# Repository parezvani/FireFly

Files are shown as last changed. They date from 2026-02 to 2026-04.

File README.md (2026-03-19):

# ESP-32-Drone (FireFLY)

FireFLY is a student-built drone platform centered on the `ESP32-C3-DevKit-RUST-1` for fire risk monitoring in areas without existing sensor coverage.

## Need
Remote and high fire-risk areas lack the sensor infrastructure necessary to monitor environmental conditions during the critical pre-fire window, leaving fire response teams without the real-time data needed to act early.

## Goal
Provide fire response teams with real-time temperature, humidity, and smoke readings from high-risk, infrastructure-free terrain by deploying a rapidly mobilized monitoring system that transmits real-time data to a ground station and alerts operators when fire risk thresholds are crossed.

## Repository Layout
- `main/`: source code, firmware experiments, and hardware tests.
  - `scripts/`: ESP-NOW communication and control prototypes.
  - `base-server/fire-server/`: Rust ground-station server/client for telemetry.
  - `testing/motor/`: motor test firmware and hardware validation code.
  - `lab4_1/`: earlier lab firmware kept for reference.
  - `scrapped/`: older discarded experiments and scratch files.
- `docs/`: project documentation and design artifacts.
  - `drone-designs/`: CAD models, frame iterations, and dimensions.
  - `circuit-design/`: wiring diagrams, schematics, and circuit photos.
  - `bill-of-materials/`: BoM revisions and pricing snapshots.
  - `design-document/`: LaTeX source and exported design document PDFs.
  - `status-reports/`: progress reports and planning artifacts.
  - `meeting-notes/`: team notes, decisions, and action items.
  - `research-notes/`: reference material gathered during development.
- `esp/esp-idf/`: local checkout of the ESP-IDF framework used by the embedded work.

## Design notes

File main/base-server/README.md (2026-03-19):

FIRE_SERVER:
------------------------------------------------------------------------------------------------------------------------------------------
Sends message using cargo/rust. 
If you want to test this out on your own you can download the "fire_server" directory. 

Open two instances of Ubuntu:
- On one run "cargo run --bin fire_server", 
- On the other run "cargo run --bin fire_server"

Send message from drone to server in the following format:
- Request Line: FIRE /telemetry DRONE/1.0\n
- Telemetry Line: Fire-Detected: yes; Fire-Distance: 120; Fire-Range: 45; Temperature: 63.4; Humidity: 21.5; Drone-ID: DRONE-01\n

Full Payload:
FIRE /telemetry DRONE/1.0\nFire-Detected: yes; Fire-Distance: 120; Fire-Range: 45; Temperature: 63.4; Humidity: 21.5; Drone-ID: DRONE-01\n

------------------------------------------------------------------------------------------------------------------------------------------
------------------------------------------------------------------------------------------------------------------------------------------

ESPNOW DIRECTORIES:
------------------------------------------------------------------------------------------------------------------------------------------
Sends messages between two ESP32c3-devkit-Rust-1 microcontrollers
Uses ESP-IDF

Build and flash fire_bridge on base station esp

Build and flash fire_drone on drone esp

Currently takes temperature and humidity readings from onboard drone ESP IMU and sends them to the base server ESP through ESP-NOW

Same payload construction as fire_server:
FIRE /telemetry DRONE/1.0\nFire-Detected: yes; Fire-Distance: 120; Fire-Range: 45; Temperature: 63.4; Humidity: 21.5; Drone-ID: DRONE-01\n

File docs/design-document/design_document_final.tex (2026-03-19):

\documentclass[journal, onecolumn]{IEEEtran}

\usepackage{titlesec}
\usepackage{graphicx}
\usepackage{array}
\usepackage{makecell}
\usepackage{float}
\usepackage{caption}
\usepackage{wrapfig}

\titleformat{\section}
    {\normalfont\bfseries}
    {\thesection}
    {1em}
    {}

\titleformat{\subsection}
    {\normalfont\bfseries}
    {\thesubsection}
    {1em}
    {}

\renewcommand\thesection{\arabic{section}}
\renewcommand\thesubsection{\thesection.\arabic{subsection}}
\renewcommand\thesubsubsection{\thesubsection.\arabic{subsubsection}}

\begin{document}

\title{FireFly Design Document}
\author{Christian Li, Kenny Wang, Kevin Yao, Matin Sobhani, Nick Lafredo, Parsa Rezvani, Ryan Yu}
\date{\today}

\maketitle

\begin{figure*}[!t]
    \centering
    
    \caption*{}
    \label{fig:UCSCLOGO}
\end{figure*}

\vspace{1in}

\begin{figure*}[!t]
    \centering
    
    \caption*{}
    \label{fig:BELOGO}
\end{figure*}

\clearpage

\tableofcontents

\vspace{1in}

\begin{abstract}
This document presents the design and proof-of-concept for FireFly, a rapidly deployable environmental monitoring drone for wildfire detection in infrastructure-free terrain.
\end{abstract}

\newpage

% ============================================================
\section*{Executive Summary}
\addcontentsline{toc}{section}{Executive Summary}
% ============================================================

FireFly is a rapidly deployable quadcopter designed for first-response
environmental monitoring in high wildfire-risk areas with no existing sensor
infrastructure. The system collects real-time temperature, humidity, and smoke
data and transmits live readings to a ground station, triggering alerts when
fire risk thresholds are crossed.

\vspace{0.5em}

The design centers on a 3D-printed X-frame carrying a dedicated onboard microcontroller, temperature and humidity sensor, and smoke detector. A flight controller manages propulsion and stabilization while the onboard microcontroller handles sensor acquisition and wireless transmission to a ground receiver. A 3S LiPo battery powers both propulsion and electronics for the duration of a monitoring mission.

\vspace{0.5em}

Validation consists of bench testing individual modules (power, propulsion,
sensors, and communications) followed by tethered and open-field flight
testing for stable hover, data link verification, and threshold-based smoke
and temperature detection. The goal is to demonstrate that FireFly can serve
as a practical proof-of-concept for infrastructure-independent wildfire
monitoring.

\clearpage

% ============================================================
\section{Introduction}
% ============================================================

This document contains all the information needed to design and use the FireFly Drone.

\vspace{1em}

Why is collecting data during a pre-fire window important? A pre-fire window, the period before an incident occurs, is critical because it provides time-sensitive information that improves responder safety, reduces property damage, and enables faster, more effective emergency response. Data on vegetation conditions, topography, temperature, humidity, and smoke concentration helps predict fire behavior, identify high-risk areas, and support mitigation actions such as controlled burns or targeted thinning operations. Without this information, emergency crews arrive with incomplete situational awareness and must gather critical details in real time under dangerous conditions.

\vspace{1em}

For wildfire response specifically, the challenge is compounded by geography. High-risk areas are frequently roadless wilderness where permanent sensor infrastructure cannot be installed or maintained. Satellite imagery and aerial patrols provide coverage, but both suffer from response delays and gaps during the highest-risk windows. The result is a critical blind spot: the pre-fire period in remote terrain is precisely where early awareness matters most, yet it is the hardest environment in which to collect data.

\vspace{1em}

FireFly addresses this gap directly. By deploying a sensor-equipped quadcopter into areas with zero existing infrastructure, FireFly enables real-time collection of temperature, humidity, and smoke data during the pre-fire window, transmitting live readings to a ground station and triggering alerts when fire risk thresholds are crossed. The platform is designed for rapid deployment by field crews without requiring extensive training or specialized support, transforming what would otherwise be a period of uncertainty into a structured, data-driven response.

\subsection{Need Statement}
Remote and high fire-risk areas lack the sensor infrastructure necessary to monitor environmental conditions during the critical pre-fire window, leaving fire response teams without the real-time data needed to act early.

\subsection{Goal Statement}
Provide fire response teams with real-time temperature, humidity, and smoke readings from high-risk, infrastructure-free terrain by deploying a rapidly mobilized monitoring system that transmits real-time data to a ground station and alerts operators when fire risk thresholds are crossed.

\subsection{Personas}
Individuals with experience levels ranging from novice to expert in fire monitoring and environmental fieldwork.

\subsubsection*{End Users}

\begin{wrapfigure}{l}{0.2\textwidth}
    
\end{wrapfigure}
\textbf{Marcus} \\
\underline{\textit{Role:}} Wildfire Operations Coordinator (professional first responder) \\
\underline{\textit{Background / Context:}} Works with a state forestry division managing prescribed burns and post-fire monitoring. Needs something fast that he can hand off to field crews without extensive training. \\
\underline{\textit{Goals:}} Rapid deployment of sensor-equipped drones into areas too dangerous or inaccessible for personnel during the high-risk pre-fire window. Wants real-time smoke and temperature data without putting people in harm's way. \\
\underline{\textit{Behaviors:}} Works under time pressure, values reliability over features, and coordinates with multiple agencies. Skeptical of unproven technology. Practical: if it breaks in the field, it needs to be fixable on-site with minimal tools. \\
\underline{\textit{Expectations:}} A rugged, simple-to-operate platform that can be deployed at a moment's notice. Wants clear threshold alerts he can act on immediately.

\vspace{1em}

\begin{wrapfigure}{l}{0.2\textwidth}
    
\end{wrapfigure}
\textbf{Elena} \\
\underline{\textit{Role:}} Ecology Graduate Researcher (academic user) \\
\underline{\textit{Background / Context:}} Studying fire risk and ecosystem conditions at a land-grant university. Needs to collect environmental sensor data across wilderness areas where no permanent monitoring infrastructure exists. Currently hikes in with handheld sensors, which limits how often and how broadly she can sample. \\
\underline{\textit{Goals:}} Automate pre-fire data collection over defined survey areas. Wants live temperature, humidity, and smoke readings logged without requiring physical presence at each site. \\
\underline{\textit{Behaviors:}} Comfortable with technical documentation, participates in academic drone and environmental monitoring communities, and documents everything for publication. Willing to configure and customize but does not have time to build from scratch. \\
\underline{\textit{Expectations:}} A reliable platform with a clear data pipeline she can connect to her existing research database, and results trustworthy enough to cite.

\vspace{1em}

\subsubsection*{Experts / Consultants}

\begin{wrapfigure}{l}{0.2\textwidth}
    
\end{wrapfigure}
\textbf{Dr. Anita Rowe} \\
\underline{\textit{Role:}} Environmental Sensor Systems Engineer \\
\underline{\textit{Background / Context:}} Works at a national lab developing atmospheric sensor arrays for wildfire monitoring. Has deep expertise in what data is actually actionable in pre-fire environments and where sensors fail under heat, humidity, and particulate exposure. \\
\underline{\textit{Goals:}} Validate that FireFly's sensor suite captures meaningful data for fire risk assessment and identify unreliable component choices before they are locked into the design. \\
\underline{\textit{Behaviors:}} Data-driven and skeptical of consumer-grade sensors in harsh field conditions. Will probe calibration drift, operating temperature limits, and whether threshold alert logic reflects real-world fire risk indicators. \\
\underline{\textit{Expectations:}} A platform sound enough in its sensor selection and alert logic that field results can be trusted and the methodology can be defended to other scientists.

\vspace{1em}

\subsubsection*{Client}

\begin{wrapfigure}{l}{0.2\textwidth}
    
\end{wrapfigure}
\textbf{U.S. Forest Service Regional Office} \\
\underline{\textit{Role:}} Federal Land and Fire Management Agency \\
\underline{\textit{Background / Context:}} Responsible for fire prevention, monitoring, and response across millions of acres of national forest, much of it roadless wilderness with no existing sensor infrastructure. Currently relies on satellite imagery, fire lookout towers, and aerial patrols, all of which have coverage gaps and response delays during the highest-risk windows. \\
\underline{\textit{Goals:}} Evaluate FireFly as a rapidly deployable supplement to existing monitoring systems for areas where infrastructure cannot operate. Interested in whether the platform can reliably trigger alerts before a fire establishes. \\
\underline{\textit{Behaviors:}} Evaluates tools based on operational reliability and ease of use for non-specialist field crews. Requires demonstrated performance data before recommending adoption. \\
\underline{\textit{Expectations:}} A working prototype that proves the core concept: zero-infrastructure deployment, live sensor transmission, and threshold-based alerting, with documentation clear enough for field personnel to operate without engineering support.

\subsection{Existing Research}
Current wildfire detection relies on satellite imagery, fixed camera networks,
and manned aircraft. Satellites cannot reliably detect fires smaller than
approximately 18 square kilometers. Fixed towers like AlertCalifornia's
camera network are constrained by line of sight, leaving roadless terrain
uncovered. UAV-based systems have shown promise, with UAV--IoT networks
detecting fires as small as 2.5 square kilometers at over 99 percent accuracy,
but most depend on pre-deployed ground sensors or persistent network
infrastructure that does not exist in remote areas.

\vspace{0.5em}

FireFly addresses this gap by providing a self-contained, rapidly deployable
platform that requires no pre-existing infrastructure to deliver real-time
environmental data and threshold-based fire risk alerts.

\subsection{Sustainability Statement}

The FireFly project is committed to the ``Design for Environment'' philosophy. Our goal is to provide a high-tech solution for wildfire mitigation while ensuring that the lifecycle of the drone itself does not offset its environmental benefits.

\vspace{1em}

\textbf{Environmental Stewardship:}
The primary purpose of FireFly is the preservation of biodiversity and carbon sinks by preventing catastrophic wildfires. By providing early-warning data in the pre-fire window, we reduce the need for large-scale, carbon-intensive emergency responses such as heavy tanker aircraft and ground fleets. Furthermore, by utilizing electric propulsion over internal combustion, we ensure zero-emission operation during monitoring flights.

\vspace{1em}

\textbf{Material Selection and Circularity:}
To minimize our manufacturing footprint, we have opted for 3D-printed components using \textbf{PLA}. PLA is a bio-based, industrially compostable polymer derived from renewable resources like corn starch. By using additive manufacturing, we significantly reduce material waste compared to traditional subtractive machining.

\vspace{1em}

\textbf{Life Cycle and Battery Management:}
We recognize that Lithium-Polymer (LiPo) batteries pose a chemical risk if disposed of improperly. Our operational plan includes a strict end-of-life protocol where degraded cells are discharged and taken to certified e-waste recycling centers. We have designed the electronics with standardized connectors to ensure that sensors and flight controllers can be harvested and reused in future iterations of the platform, extending the functional life of the high-value silicon components.

\vspace{1em}

\textbf{Social and Safety Impact:}
Sustainability includes the protection of human capital. FireFly enhances the safety of first responders by providing situational awareness in hazardous terrains without risking human life. By creating a rapidly deployable tool, we extend access to advanced fire-monitoring capability to smaller forestry divisions and academic researchers who operate outside the reach of satellite-based or manned aerial surveillance programs.

\vspace{1em}

\textbf{Ethics Statement:}
As engineers, we recognize that our work has a direct impact on public safety and the environment. We are committed to upholding the highest standards of honesty, transparency, and responsibility throughout the design and development of FireFly. Our system is intended solely to support fire prevention and responder safety. We will not misrepresent the capabilities of the prototype, will clearly communicate the limitations of sensor accuracy and flight duration, and will ensure that any data collected during testing is handled responsibly. We adhere to the NSPE Code of Ethics, holding paramount the safety, health, and welfare of the public in all design decisions.

% ============================================================
\section{Design}
% ============================================================

\subsection{Design Objectives}
The objective of this project is to develop a robust aerial monitoring platform capable of reliable operation in remote, high-risk environments. To achieve this, the system requires a long-range communication link and high-speed data transmission to ensure low-latency control and real-time environmental telemetry. Furthermore, the power architecture must be optimized to sustain extended monitoring missions.

\newpage

\subsection{Aesthetic Prototype}

The FireFly aesthetic prototype follows a field-ready design language: a compact enclosed central body with rounded corners, symmetric X-arm geometry, and cylindrical motor pods at each corner. The overall form emphasizes structural clarity and quick visual inspection rather than cosmetic styling. Rounded exterior edges reduce snag points during transport, while the open-top bay and side windows communicate where electronics, wiring, and battery hardware are intended to be serviced.

\begin{figure}[H]
    \centering
    
    \hfill
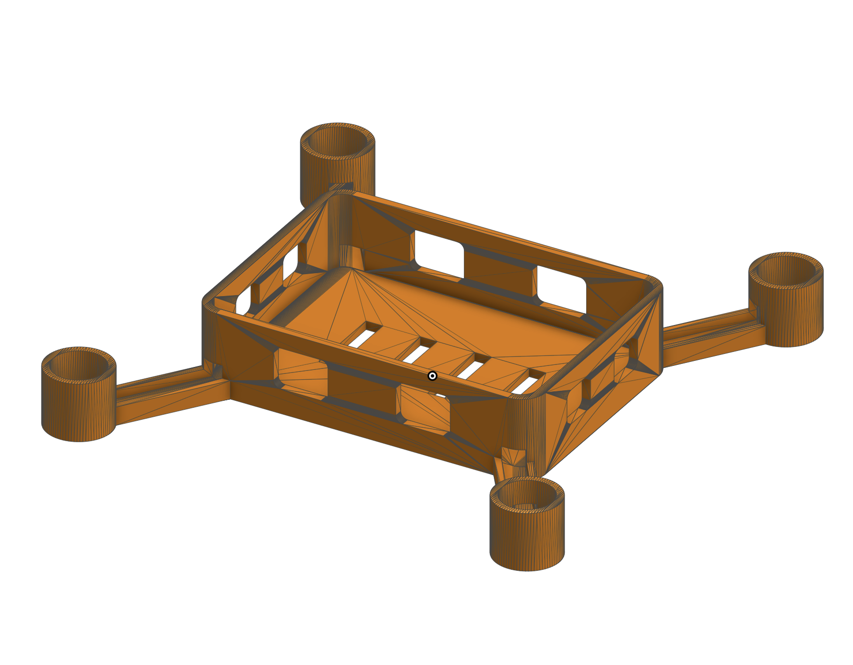
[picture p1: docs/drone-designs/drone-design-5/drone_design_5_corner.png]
    
    \caption{FireFly CAD aesthetic prototype, iteration v5 (top and isometric views).}
    \label{fig:drone_v5_aesthetic}
\end{figure}

The prototype evolved through multiple print-test iterations. Early versions validated basic packaging and motor placement, while later versions introduced a cleaner body-to-arm transition, larger internal volume, and improved vent/window geometry for lighter weight and faster access to internals. This iterative process preserved a consistent visual identity while converging on a more manufacturable and maintainable frame.

\begin{figure}[H]
    \centering
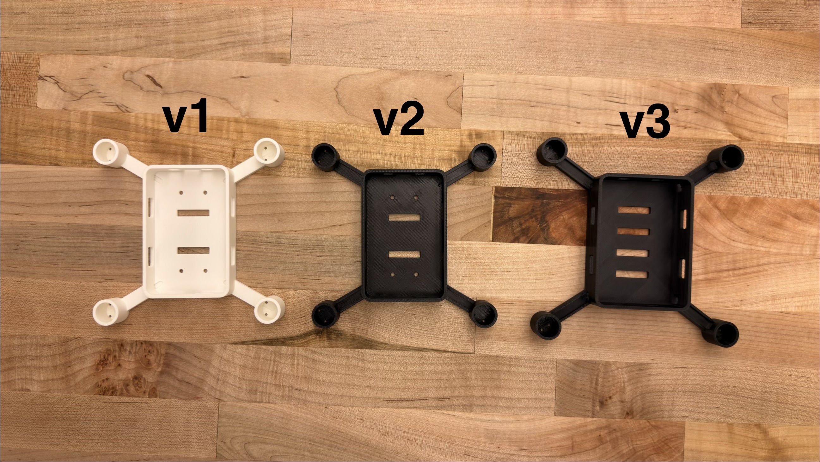
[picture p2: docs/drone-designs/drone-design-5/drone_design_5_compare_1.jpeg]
    
    \caption{Physical prototype progression (v1--v3) that informed the final v5 frame direction.}
    \label{fig:drone_proto_progression}
\end{figure}

\subsection{Design for Manufacture, Assembly, Maintenance}

\textbf{Design for Manufacture (DFM):}
The current frame is designed as a single-piece 3D print to minimize part count and remove alignment errors. The v5 CAD envelope is approximately $100 \times 72 \times 24$ mm with $2.5$ mm floor and wall thicknesses, balancing print speed, stiffness, and mass. Arms are sized at $10.0$ mm width and $5.4$ mm thickness to maintain rigidity under motor thrust and landing loads. Motor pods are dimensioned for SunnySky R1106-class motors with built-in tolerance ($19$ mm outer diameter, $15.0$ mm inner diameter, $17$ mm height, $2.2$ mm mounting holes on a $9$ mm bolt-circle).

\vspace{0.5em}

\textbf{Design for Assembly (DFA):}
Assembly features are integrated directly into the print geometry. The frame includes four battery strap slots in the floor and continuous wire-routing paths from motor pods into the electronics bay. This allows a straightforward assembly order: install motors in pods, route motor leads through arm channels, mount the controller board, then secure the battery and sensor harness. Because most interfaces are geometric rather than adhesive, rework is possible without damaging the frame.

\vspace{0.5em}

\textbf{Design for Maintenance (DFMn):}
Maintenance access is provided by the open top cavity, side-wall windows, and pod-to-arm wire notches. These features allow quick inspection of solder joints, connector seating, and wire wear without full teardown. Electronics can be removed independently from propulsion hardware, and battery straps can be replaced in the field with standard hook-and-loop straps. In case of structural damage, the one-piece architecture supports rapid replacement by reprinting the frame using the same CAD file, preserving dimensional repeatability across repairs.

\subsection{Block Diagrams}

\begin{figure}[H]
    \centering
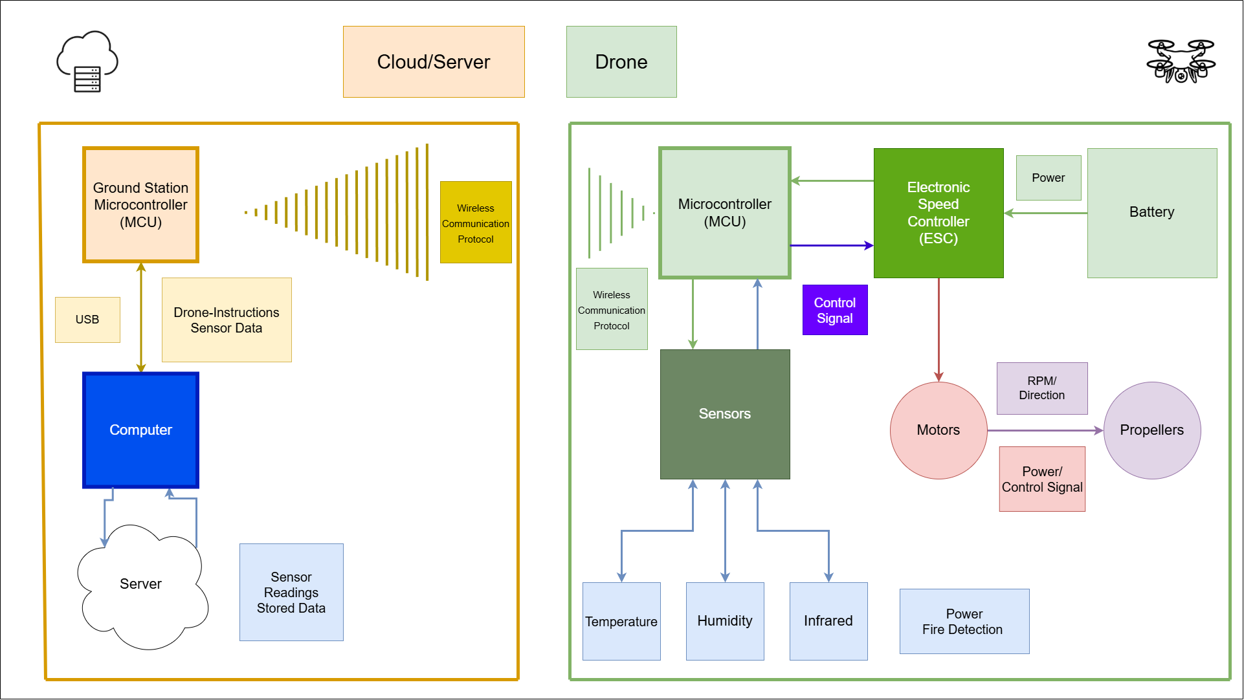
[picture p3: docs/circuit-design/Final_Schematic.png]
    
    \caption{A high-level schematic of the FireFly system.}
    \label{fig:schematic_design}
\end{figure}

\subsection{Wiring Diagrams}

\begin{figure}[H]
    \centering
    
    \caption{Circuit Diagram}
    \label{fig:circuit_diagram}
\end{figure}

\subsection{State Transition Diagrams}

\begin{figure}[H]
    \centering
    
    \caption{State Transition Diagram}
    \label{fig:state_transition}
\end{figure}

\subsection{Technology (Languages, Hardware, etc.)}

FireFly uses a two-node wireless architecture connected via a low-latency peer-to-peer radio protocol. The drone carries an onboard microcontroller that reads sensor data from a temperature and humidity sensor and a smoke detector, packages the readings into a structured telemetry packet, and transmits it wirelessly to a ground receiver. The communication link operates on the 2.4GHz band with a range of approximately 400 meters line-of-sight and latency under 10ms, making it well suited for remote wildfire monitoring scenarios where reliable low-latency telemetry is critical.

\vspace{0.5em}

The ground station consists of a second microcontroller that acts as a dedicated receiver, unpacks the incoming telemetry data, and forwards it as a JSON stream over USB serial to a host machine. The host machine runs a Python Flask server that reads the serial stream and exposes a local HTTP endpoint, which a browser-based dashboard polls at one-second intervals to display live sensor readings. Firmware on both microcontrollers is written in C, with the ground station dashboard implemented in Python and JavaScript.

\subsection{Simulations}

Before building and flying, we used simulation tools to verify that the FireFly configuration can sustain flight, carry its sensor payload, and meet the core mission requirement of delivering real-time environmental data during the pre-fire window. An online multicopter calculator (eCalc xcopterCalc) was used to evaluate combinations of frame size, motors, propellers, and battery against thrust-to-weight ratio, hover throttle, current draw, and expected flight time under sensor payload assumptions. This confirmed that the selected hardware provides sufficient thrust margin to carry the temperature/humidity sensor and smoke detector while maintaining acceptable hover efficiency and a flight time long enough to collect and transmit meaningful readings to the ground station.

\vspace{0.5em}

A simplified quadcopter dynamics model was used to tune attitude and altitude control parameters, verifying that the platform can hold a stable position over a monitoring area, a prerequisite for consistent sensor sampling. Research on quadcopter modeling confirms that such simulations can predict controller behavior and reduce the number of risky test flights needed to achieve stable flight. Together, these simulations provide evidence that FireFly can meet its need statement requirements: reaching areas with zero sensor infrastructure and sustaining flight long enough to collect and transmit temperature, humidity, and smoke data before committing to full implementation and field testing.

\newpage

% ============================================================
\section{Evaluation}
% ============================================================

\subsection{Functional Prototype}
As of the initial submission, FireFly's functional prototype is currently under assembly. Core components, including the onboard microcontrollers, temperature and humidity sensor, and smoke detector, have been sourced and bench-tested for communication and sensor output. A prototype circuitry system using an H-Bridge in place of the ESC and a DC brushed motor in place of the brushless motor was assembled to validate the wireless communication link between the ground-side and drone-side microcontrollers while awaiting final parts. Full integration with the flight stack and ground station dashboard is in progress. Photographs and detailed performance data will be included in the final Spring Quarter submission.

\subsection{Testing}
Initial bench testing has validated point-to-point wireless communication between the drone-side and ground-side microcontrollers, confirmed sensor readout from the temperature/humidity and smoke sensors, and verified JSON telemetry forwarding over USB serial to the Flask dashboard. Full tethered and open-field flight testing with threshold-based alert verification is planned for the prototype phase. Detailed test procedures and results are documented in Appendix 3.

\newpage

% ============================================================
\section{Parts List}
% ============================================================

\begin{table}[H]
    \centering
    \small
    \begin{tabular}{|l|c|c|}
        \hline
        \textbf{Part} & \textbf{Supplier} & \textbf{Quantity} \\
        \hline
        CarbonX PLA+CF Filament & Creality & 1 \\
        \hline
        Battery: LiPo 850 mAh 3S 25/30C & HobbyKing & 1 \\
        \hline
        Motor: SunnySky R1106 FPV Brushless Motors & Druav & 4 \\
        \hline
        Propeller: Gemfan Hurricane 2009-3 Tri-Blade (Set of 4) & Pyrodrone & 1 \\
        \hline
        HAKRC 20A 4-in-1 \verb|3-6S BLHeli_32| 5V 3A BEC DShot1200 Mini ESC & Alibaba & 1 \\
        \hline
        Perforated Circuit Board & Adafruit & 2 \\
        \hline
        Female Header Pins 2x6 & AliExpress & 4 \\
        \hline
        Female Header Pins 2x8 & AliExpress & 2 \\
        \hline
        Female Header Pins 2x10 & Mikroe & 2 \\
        \hline
    \end{tabular}
    \caption{Itemized Parts List}
    \label{tab:budget}
\end{table}

\newpage

% ============================================================
\section{Appendix 1 - Problem Formulation}
% ============================================================

\subsection{Conceptualisations}

FireFly is a lightweight quadcopter designed to collect and transmit
environmental sensor data in remote areas with no existing infrastructure.
The system is built around three functions: stable flight, environmental
sensing, and real-time data transmission.

\vspace{0.5em}

The drone carries an onboard microcontroller paired with a temperature and humidity sensor and a smoke detector. A flight controller manages propulsion and stabilization while the onboard microcontroller handles sensor acquisition and wireless transmission. A LiPo battery powers both propulsion and electronics for the duration of a monitoring mission.

\vspace{0.5em}

Data is transmitted wirelessly to a ground receiver microcontroller, which forwards readings over USB serial to a host machine running a Python Flask dashboard displaying live sensor data and threshold alerts.

\subsection{Brainstorming}
Several frame geometries were evaluated including X and H-style quadcopter
layouts. An X-frame was selected for its balanced motor distribution,
stability, and ease of sensor mounting.

\vspace{0.5em}

The sensing approach was inspired by existing ground-based forest sensor
networks, which are geographically limited and difficult to scale into remote
terrain. FireFly was conceived as a mobile alternative: a drone that could
collect the same environmental data in areas where fixed infrastructure does
not exist.

\vspace{0.5em}

For communication, Bluetooth Low Energy and Wi-Fi were both evaluated. A connectionless peer-to-peer wireless protocol was ultimately selected for its simplicity, low latency, and sufficient range for a point-to-point link between the drone and ground receiver without the overhead of a full Wi-Fi stack.

\vspace{0.5em}

Power and propulsion options were compared using eCalc to evaluate
thrust-to-weight ratio, hover current, and projected flight time across
different motor, propeller, and LiPo configurations. This guided selection
of a 3S LiPo and motor pairing that balances flight endurance with the
electrical load of the sensor and communication hardware.

\subsection{Decision Tables}

The following decision tables evaluate key design alternatives across weighted criteria. Scores are rated 1--5 per criterion, multiplied by the criterion weight, and summed to produce a weighted total.

\begin{table}[H]
\centering
\small
\begin{tabular}{|l|c|c|c|c|}
\hline
\textbf{Criterion} & \textbf{Weight} & \textbf{X-Frame} & \textbf{H-Frame} & \textbf{+ Frame} \\
\hline
Stability & 25\% & 5 & 3 & 4 \\
\hline
Sensor Mounting & 20\% & 5 & 4 & 3 \\
\hline
Ease of Assembly & 20\% & 4 & 4 & 3 \\
\hline
Printability & 20\% & 4 & 3 & 5 \\
\hline
Repairability & 15\% & 4 & 5 & 3 \\
\hline
\textbf{Weighted Total} & & \textbf{4.45} & \textbf{3.75} & \textbf{3.65} \\
\hline
\end{tabular}
\caption{Frame Geometry Decision Table}
\end{table}

\begin{table}[H]
\centering
\small
\begin{tabular}{|l|c|c|c|c|}
\hline
\textbf{Criterion} & \textbf{Weight} & \textbf{Peer-to-Peer Wireless} & \textbf{Wi-Fi} & \textbf{BLE} \\
\hline
Latency & 30\% & 5 & 3 & 4 \\
\hline
Range & 25\% & 5 & 4 & 2 \\
\hline
Infrastructure Required & 25\% & 5 & 2 & 4 \\
\hline
Implementation Complexity & 20\% & 4 & 3 & 4 \\
\hline
\textbf{Weighted Total} & & \textbf{4.80} & \textbf{3.00} & \textbf{3.50} \\
\hline
\end{tabular}
\caption{Communication Protocol Decision Table}
\end{table}

\begin{table}[H]
\centering
\small
\begin{tabular}{|l|c|c|c|}
\hline
\textbf{Criterion} & \textbf{Weight} & \textbf{PLA} & \textbf{Carbon Fiber PLA} \\
\hline
Weight & 30\% & 4 & 5 \\
\hline
Printability & 25\% & 5 & 3 \\
\hline
Structural Rigidity & 25\% & 3 & 5 \\
\hline
Repairability & 20\% & 5 & 3 \\
\hline
\textbf{Weighted Total} & & \textbf{4.20} & \textbf{4.00} \\
\hline
\end{tabular}
\caption{Frame Material Decision Table}
\end{table}

\subsection{Morphological Charts}
The following combinations were explored for the primary subsystems:
\begin{figure}[H]
    \centering
    
    \caption{Morphological analysis chart outlining potential components of FireFly}
    \label{fig:morphological}
\end{figure}

\newpage

% ============================================================
\section{Appendix 2 - Planning}
% ============================================================

\subsection{Basic Plan / Gantt Chart}
\begin{figure}[H]
    \centering
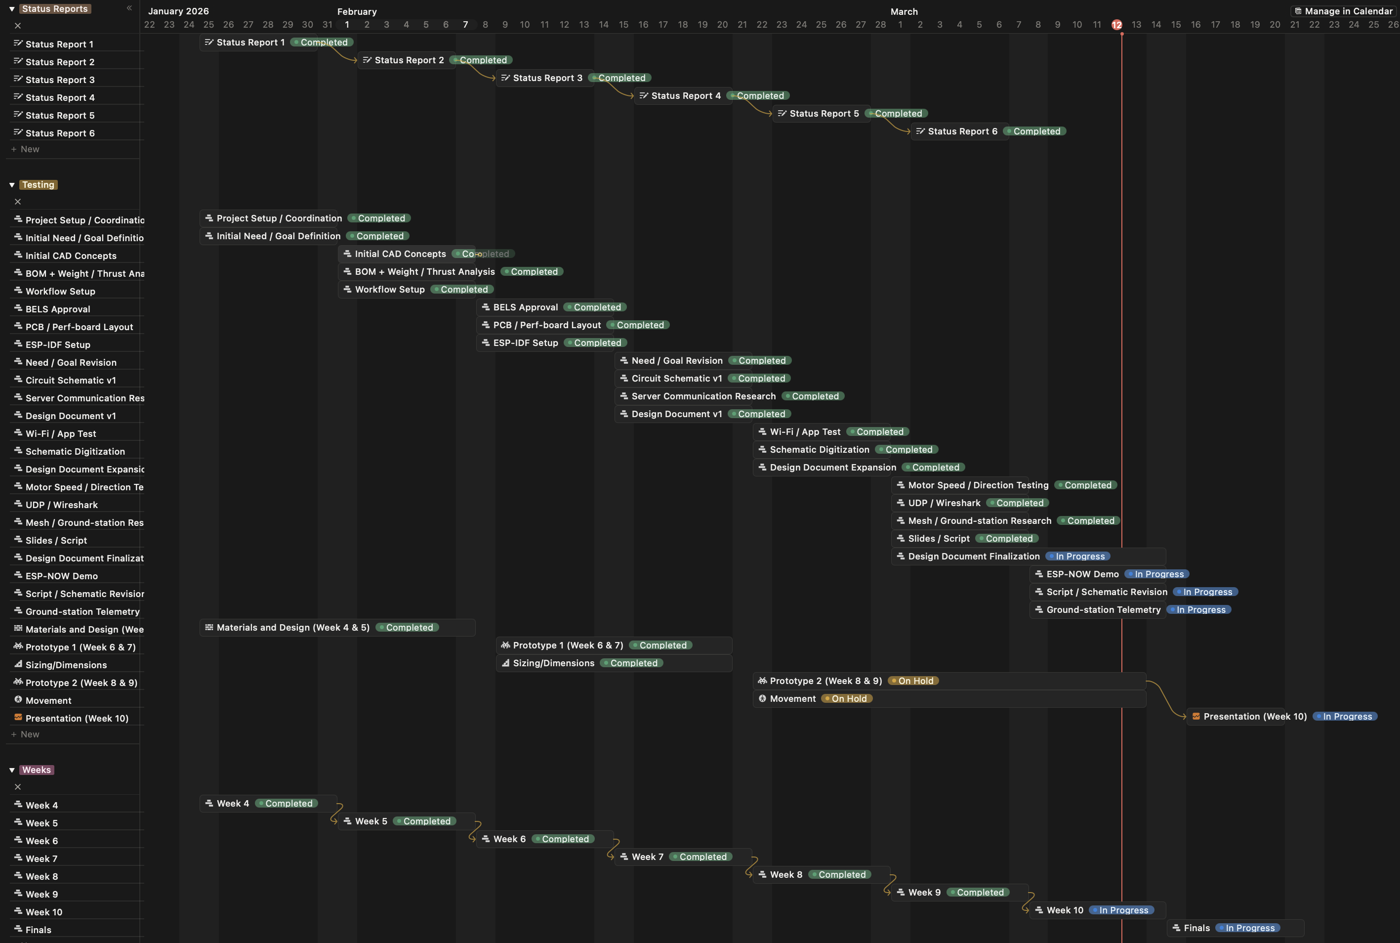
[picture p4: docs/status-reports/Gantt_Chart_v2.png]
    
    \caption{Gantt Chart}
    \label{fig:gantt_chart}
\end{figure}

\subsection{Division of Labor}

\begin{table}[H]
    \centering
    \begin{tabular}{|l|l|}
        \hline
        \textbf{Team Member} & \textbf{Primary Responsibility} \\
        \hline
        Christian Li & Flight Controller Programming \\
        \hline
        Kenny Wang & Hardware Integration \\
        \hline
        Kevin Yao & Mechanical Design / CAD \\
        \hline
        Matin Sobhani & Mechanical Design / CAD \\
        \hline
        Nick Lafredo & Power Systems / Documentation \\
        \hline
        Parsa Rezvani & Testing and Validation / Telemetry \\
        \hline
        Ryan Yu & Flight Controller Programming \\
        \hline
    \end{tabular}
    \caption{Division of Labor during Prototyping}
\end{table}

\subsection{Collaboration}
\begin{itemize}
    \item \textbf{Github:} CI/CD Tool
    \item \textbf{Discord:} Communication and meetings
    \item \textbf{Notion:} Gantt Chart
    \item \textbf{Trello:} Kanban board for task tracking
\end{itemize}

\newpage

% ============================================================
\section{Appendix 3 - Test Plan \& Results}
% ============================================================

The test plan consists of three phases:
\begin{enumerate}
    \item \textbf{Bench Testing:}

    We began by creating a prototype circuitry system that utilizes an H-Bridge in substitution for the Electronic Speed Controller, along with a DC brushed motor in place of the designed DC brushless motor. This system was used to test the wireless communication between the ground-side and drone-side microcontrollers, allowing us to develop and validate the data transmission pipeline while awaiting final parts.

    \item \textbf{Tethered Flight:}

    We will integrate the ESC and DC brushless motors into the physical 3D-printed frame and test flight capability in a controlled indoor environment. During this phase we will emulate conditions that would flag a fire danger zone (elevated temperature, low humidity, and elevated smoke readings) and verify that threshold alerts are correctly triggered and transmitted to the ground station.

    \item \textbf{Open Field Flight:}

    We will test the drone in an open field to evaluate durability, structural integrity, and real-world sensor performance. Outdoor conditions including wind and heat will allow us to assess how environmental factors affect flight stability and sensor accuracy, providing direct feedback on both the mechanical design and the telemetry pipeline under realistic deployment conditions.
\end{enumerate}

\newpage

% ============================================================
\section{Appendix 4 - Review}
% ============================================================

\textit{Reflection of each team member's thoughts on the project.}

\vspace{1em}

\textbf{Christian Li:} Looking back on this project, one of the biggest lessons I learned is the importance of starting with a clearly defined need rather than a preconceived solution. We approached the project wanting to build a drone, and only later did we step back and ask why a drone was the right solution for the problem. If we had focused earlier on the lack of fire risk data in remote areas, we could have identified the required characteristics sooner and avoided some of the design and task adjustments we made midway through the quarter. Even so, our team communicated well and adapted quickly. The flexibility helped us stay on track and produce a coherent design. This experience also gave me valuable insight into working as a team, improving how we communicate, distribute work, and learn new tools and environments together.

\vspace{1em}

\textbf{Kenny Wang:} Restarting this project I think that we should focus on not building a product that interests us but develop the idea based on a universal problem or a need. From there we can then focus on implementing it in a way that can handle this universal problem or need. For example, if we had started with the problem being that we have no way of reaching remote areas with no fire detection, we can then build upon that and not just specifically building a flying drone but maybe a rover, or even something that does not even have to move. There would be a variety of implementations of helping alleviate the same problem and need while having numerous amounts of angles to implement that solution. Even with some setbacks that we faced during the beginning stages of the project we were able to have good communication within the team to implement these changes so that we were able to complete our design work.

\vspace{1em}

\textbf{Kevin Yao:} Reflecting back to the beginning of this project, I think we should have focused on the process instead of the end goal of the design we wanted to make. One thing that we did well was forming our group and communicating often. We were vocal on what we wanted to do and had ideas on what the design would look like. A problem that occurred was our need and goal statement. What we should have done differently was to define clear objectives of what needed to be done and check the requirements. Another thing we should have done earlier was setting up the github with our other tools to have a cleaner pipeline of our progress. Although we had some setbacks, our team was able to implement these changes quickly and improved our communication and workflow.

\vspace{1em}

\textbf{Matin Sobhani:} If we were starting this project again, I would make sure we had a solid need/goal statement, and verified it with the TA and professor. We thought we had a solid one early on around week 4, but ended up having to change it around week 8. Thankfully this did not affect us too negatively since our underlying prototype idea stayed mostly the same, but it did cost us time and forced us to reframe parts of our documentation. In hindsight, we should have scheduled a formal requirement check-in earlier and created clearer milestones tied to those requirements so we could catch misalignment sooner. What went well is that we stayed very communicative throughout the project, kept each other up-to-date, and adapted quickly whenever priorities changed.

\vspace{1em}

\textbf{Nick Lafredo:} This project is the first I've done on such a large scale, and it taught me a lot about the timeline and organization needed to accomplish a group goal. If we were to go back and start a new project, we would focus more on the need and solution, rather than starting with a product we wanted to make and finding a need that fits it. It is also now much clearer that we are not designing the prototype, but creating a general design that could be implemented in the future, with the prototype proving its possibility. We faced a few setbacks with our design and deciding what problem we were aiming to solve, but ultimately, it made our final idea much stronger and well-defined. Going forward, we will have more frequent check ins with our team and our instructors to make sure we stay on the right track. We now have a clear path towards completing the design, and I am confident that we will reach our goal.

\vspace{1em}

\textbf{Parsa Rezvani:} This project has been a significant learning experience for both me and the team. Initially, we approached it as an exercise in selecting an interesting idea and producing documentation around it. Over time, however, we came to understand that the class demanded something closer to real-world engineering practice: defining a defensible need, building toward a clear goal, and maintaining a concept that could stand on its own merits in a professional context. Had we internalized that framing earlier, our process would have been more focused from the start. Despite the adjustments along the way, I am proud of how the team collaborated and adapted. With our components arriving soon, I am confident we are well positioned to make meaningful progress on the prototype.

\vspace{1em}

\textbf{Ryan Yu:} Looking back at the beginning of this project, there are a few things that went well and a few things that went poorly. I think we got our group together, talked about initial parts, calculations, and ideas quite early, and were on top of things. However, I think the communication between the professor, TA, and our group was extremely poor. It was not clearly laid out that we were designing a product but producing a prototype. We had difficulties having useful long discussions with the professor and were often confused on what he wanted, constantly changing last minute.

\end{document}

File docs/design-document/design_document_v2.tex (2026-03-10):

\documentclass[conference]{IEEEtran}

\usepackage{titlesec}
\usepackage{graphicx} % Required for inserting images
\usepackage{array} % Required for text wrapping in tables
\usepackage{makecell}
\usepackage{float}

\titleformat{\section}
  {\normalfont\bfseries}   % bold, normal font size
  {\thesection}            % section number
  {1em}                    % space between number and title
  {}                       % before-code (empty = left aligned)

\titleformat{\subsection}
  {\normalfont\bfseries}
  {\thesubsection}
  {1em}
  {}

\renewcommand\thesection{\arabic{section}}
\renewcommand\thesubsection{\thesection.\arabic{subsection}}
\renewcommand\thesubsubsection{\thesubsection.\arabic{subsubsection}}

\begin{document}

\title{SpectreFLY Design Document}
\author{Christian Li, Kenny Wang, Kevin Yao, Matin Sobhani, Nick Lafredo, Parsa Rezvani, Ryan Yu}
\date{\today}

\maketitle
\tableofcontents

\vspace{1in}

\begin{abstract}
This document aims to teach the reader how to create the SpectreFLY Modular Drone.
\end{abstract}

\begin{IEEEkeywords}
none
\end{IEEEkeywords}

\clearpage

\section{Introduction}
This document contains all the information needed to design and use the SpectreFLY Modular Drone.
[more later]

\section{System Requirements}
[functional requirements.]

[payload, flight time, range, sensor capabilities.]

\section{System Architecture}
[overall block diagram.]

[flight controller, power, propulsion, communication, sensor bus.]

\section{Mechanical Design}
[frame layout and mounting points for motor, battery, ...]

\section{Power and Propulsion Modules}
[information about motors/propellers.]

\section{Sensor and Payload Modules}
[information about supported sensors (LiDAR, camera, ...), maximum excess payload, etc.]

\section{Electronics and Control}
[how to control the drone, what is needed for control, etc.]

\section{Modularity and Maintainability}
[information about how to swap parts, what can be swapped, and how.]

\section{Safety and Reliability}
[testing logs and proof that it can take damage and handle failures.]

[physical safety information: prop guards, connector keying to avoid misplugging.]

\section{Testing and Validation}
[bench tests for each module.]

[flight tests and criteria.]

\section{Parts List}

\begin{table}[H]
    \centering
    \small
    \begin{tabular}{|>{\raggedright\arraybackslash}p{0.3\linewidth}|c|c|c|}
        \hline
        \textbf{Part} & \textbf{Set} & \textbf{Supplier} & \textbf{Quantity} \\
        \hline
        CarbonX PLA+CF Filament & A & Creality & 1 \\
        \hline
        Battery: LiPo 850 mAh 3S 25/30C & A & HobbyKing & 1 \\
        \hline
        Motor: SunnySky R1106 FPV Brushless Motors & A & Druav & 4 \\
        \hline
        Propeller: Gemfan Hurricane 2009-3 Tri-Blade (Set of 4) & A & Pyrodrone & 1 \\
        \hline
        Battery: 3S 1000 mAh & B & HobbyKing & 1 \\
        \hline
        Motor: RCINPOWER GTS 1204 5000KV & B & Pyrodrone & 4 \\
        \hline
        Propeller: HQProp T3.5x2x3 & B & GetFPV & 1 \\
        \hline
        Caddx Ant Lite Analog Camera (FPV Cycle Edition) & A / B & CaddxFPV & 1 \\
        \hline
        TFMini-S Micro LiDAR Module & A / B & SparkFun & 1 \\
        \hline
        HAKRC 20A 4-in-1 \verb|3-6S BLHeli_32| 5V 3A BEC DShot1200 Mini ESC & A / B & Alibaba & 1 \\
        \hline
        Perforated Circuit Board & A / B & Adafruit & 2 \\
        \hline
        Female Header Pins 2x6 & A / B & AliExpress & 4 \\
        \hline
        Female Header Pins 2x8 & A / B & AliExpress & 2 \\
        \hline
        Female Header Pins 2x10 & A / B & Mikroe & 2 \\
        \hline
    \end{tabular}
    \caption{Itemized Budget}
    \label{tab:budget}
\end{table}

\end{document}

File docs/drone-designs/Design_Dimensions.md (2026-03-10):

## Drone_design_1:
- Body:
- W: 22.86mm 
- L: 63.5mm 
- H: 4.91mm
- 1.6mm Height for board

## USB-C Port:
- W: 8.94mm
- L: 7.71mm 
- H: 3.3mm

## Receiver:
- W: 13.2mm 
- L: 16.6mm 
- H: 0.8

## Chip:
- W: 11.95mm 
- L: 9.95mm 
- H: 1.755mm

## Drone Frame:
- W: 40mm (23 + (8.5 * 2))
- L: 80.5mm
- H: 10mm (Account for pins, pcb, battery, etc)

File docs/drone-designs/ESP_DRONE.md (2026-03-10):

- ESP: 9g
- Frame: 30g
- Motors: 7.5g \* 4 = 30g
- Prop: 5g
- Battery: 69g 
- Ovearhead: 200g

## OPTION A:
- Battery: LiPo 850 mAh 3s 25/30C	[link](https://hobbyking.com/en_us/turnigy-nano-tech-850mah-3s-25-40c-lipo-pack.html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)	**$6.18**	

- Motor: SunnySky R1106 FPV Brushless Motors [link1](https://sunnyskyusa.com/products/r1106) [link2](https://druav.com/products/sunnysky-r1106-fpv-motors) **$11.99 \* 4 = 47.96**	

- Propeller: Gemfan Hurricane 2009-3 Tri-Blade [link](https://pyrodrone.com/products/gemfan-2512-2-5inch-3-blade-1-5mm-2mm-hole-propeller-4cw-4ccw) **$4.99**

- AUW (baseline): ~190 – 230g

- Payload comfort: 0 – 75g

- Hover throttle: ~40 – 50%

- Real flight time: 5 – 8 minutes

- Very smooth, beginner-friendly behavior		
  
## OPTION B:
- Battery: 3S 1000 mAh [link](https://hobbyking.com/en_us/turnigy-1000mah-3s-40c-lipo-pack-jst.html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) **$10.99**

- Motor: RCINPOWER GTS 1204 5000KV Motor [link](https://pyrodrone.com/products/rcinpower-gts-1204-5000kv-motor-choose-color) **$18.99 \* 4 = 75.96**

- Propeller: HQProp T3.5x2x3 Propeller [link](https://www.getfpv.com/hqprop-3520-3-blade-1-5mm-shaft-propeller-set-of-4-grey.html) **$3.99**

- AUW (baseline): ~230 – 270 g

- Payload sweet spot: 0 – 100 g

- Hover throttle: ~35 – 45%

- Real flight time: 6 – 10 minutes depending on payload

- Cool motors, clean power for ESP

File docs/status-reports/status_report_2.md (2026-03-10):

# Status Report 2

## Achievements:
- Got SolidWorks key from BELS.
- Completed CAD sketch in On-Shape.
- Integrated kanban into Trello.
- Established a finalized needs goal and problem statement.
- Building a materials list.
- Built a theoritcal weight for all of the components combined together.

## Setbacks:
- Running into "running out of free blocks" issue in Notion. May need to change to a different collaboration tool.
- Learning curve with On-Shape and using the 3D modeling system for the first time.
- Finding parts that will not exceed a certain price point.
- Finding parts that work together.
- Working thorugh the different delivery times.

## Toolsets:
- [eCalc](https://ecalc.ch) to determine exact thrust, weight, and hover time.
- Look up table for Motor & Prop Sizes: [Oscar Liang](https://oscarliang.com/table-prop-motor-lipo-weight/)

## Materials/Parts:
- **Prop**: T-Motor T76 3 Inch Ducted Propeller - Tri-Blade 
- **Motor**: SunnySky R1106 FPV Brushless Motors
- **Controller**: ESP32-c3 Rust1
- **Battery**: lipo 4s 1800mah 80/120c
- **PCB**: TBD

## Weight Distribution:
- **ESP**: 9g
- **Frame**: 30g
- **Motors**: 7.5g * 4 = 30g
- **Prop**: 5g
- **Battery**: 161g - 213g
- **PCBL**: 10g
- **Ovearhead**: 200g

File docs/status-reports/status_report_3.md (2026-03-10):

# Status Report 3

## Achievements from before:
- Finished Material list
- Finalized our CAD design

## Setbacks from before:
- Delivery of the materials might take too long to arrive

## Who Did What:
- **Christian**:
    - Imported ESP-IDF files to main branch
    - Picked up female pins and blank circuit for measurements and design from BELS
    - Worked on part decision and testing simulation on ensuring drone flight
    - Helped review 3D printed designs providing feedback and testing durability
- **Kenny**:
    - Picked up a blank circuit board to take measurements and place the drawing model on top of the CAD model the CAD team designed
    - Finalized the circuitry components necessary to build the drone
    - Working on the circuit diagram to wire everything together
- **Kevin**:
    - Made drone_design_1 in Onshape.
    - 3D Printed drone_design_1 and drone_design_5.
        - Ran into problems setting up 3D Printer.
        - Printer air printing and had to adjust filament stuck near nozzle.
    - Compared printed designs for sizing and dimensions of parts.
- **Matin**:
    - Made drone_design_2 but decided as a group it wouldn't work and was a bad design.
    - Made drone_design_5 in Onshape and [OpenSCAD](https://openscad.org).
    - Improved upon drone_design_5 based on group feedback.
        - Thinner, lighter, and longer motor arms.
    - Agreed upon drone name "SpecterFLY".
- **Nick**:
    - Made bill_of_materials_v4 to update and include perforated circuit boards and female header pins.
    - Picked up perforated circuit boards and female header pins from BELS.
    - Working with Kenny on circuit design.
        - Started Experimenting with layout of header pins + esp32c3 board
    - Improved timeline organization on Trello Board.
- **Parsa**:
    - Organized Trello Board, to see what everyone will be working on
    - Worked on the ESP-IDF files to import to main Branch
    - Planned our next steps on what we will be working on to stay on track
    - Help review part diagram to see what connections we'll need to connect all the parts of the system

- **Ryan**:
    - Finished the Persona documents
    - Made and sent the Bill of Materials to Bells and Professor Harrison
    - Sent follow up email to get approval

## To-do, In-progress, Done:
- **To-do**:
    - Design a way to implement the circuit to be hot swappable
    - Make the wires as a pin fixture instead of individual wire strands
- **In-progress**:
    - Awaiting of approval of parts sent over to BELS
    - Development of circuit diagram to wire the battery and motors
    - Finalizing the shape/body of the drone
- **Done**:
    - Sent in the BOM to BELS

## Toolsets:
- GitHub
- eCalc
- online tutorials

## Final Materials/Parts:
- Battery: LiPo 850 mAh 3s 25/30C
- Motor: SunnySky R1106 FPV Brushless Motors
- Propeller: Gemfan Hurricane 2009-3 Tri-Blade
- Camera: CADDXFPV Ant Lite Analog Camera (FPV Cycle Edition)
- Sensor: TFMini-S - Micro LiDAR Module
- ESC: HAKRC 20A 4In1 3-6S Blheli_32 5V 3A BEC Dshot1200 Mini Size ESC
- circuitry: Perforated Circuit Board

## Weight Distribution:
- ESP: 9g
- Frame: 30g
- Motors: 7.5g * 4 = 30g
- Prop: 5g
- Battery: 69g

## Prototype 1 Presentation
- Electrical Team (Kenny and Nick)
- Software Team (Ryan, Parsa, and Christian)
- Hardware Team (Kevin, Matin, and Parsa)
- We will be explaining the needs, goals, and the audience.
- We will then go on to explain the process of how we planned and built it.
- Then we will talk about our future goals with what we are thinking of adding or revising.
- Finally look for any feedback from our audience and see if there is anything that we can do to imporve our implmentation.

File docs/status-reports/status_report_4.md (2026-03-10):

# Status Report 4

## Achievements from before:
- Updating of needs statement talk about the implementation of wireless communication with the use of smartphones
- Refining our objective design
- Printed a new body for the frame design
- Got rid of the affordability aspect of our need statement

## Setbacks from before:
- Can not order off Alibaba
- Waiting on parts
- Need to find a new ESC
- FPV Camera Compatibility issues with ESP

## Who Did What:
- **Christian**:
    - Researched bluetooth connections to ESP32, necessary PID, SPI for internal communication with IMU
    - Researched possible ESC alternatives for replacement
    - Started coding IMU communication with ESP using SPI
- **Kenny**:
    - Completed the finalized circuit design
    - Researched the ESC component for replacement
- **Kevin**:
    - Iterated drone_design_1 and made drone_design_1_2 https://cad.onshape.com/documents/2f8d4bf0b98d0485fa75c2aa/w/5e7ce9715864a154fc551824/e/40c0eff1e2915fcc79ae984e
        -  Added a cover for the drone case using a dovetail design
        -  Made a channel in the motor housing and casing for motor wires
        -  Researched dimensions of drone motor to properly fit screws and allow spacing of wires  
    - Printed out CAD models of LIPO battery and motors to test fitting of drone designs
- **Matin**:
    - Fixed drone_design_5.
        - Taller frame to account for battery, ESP-32, ESC, etc.
        - Removed motor arm channels intended for wire routing (too small/thin). Will route wires on top of the arms instead.
        - Added motor-to-frame notches/holes for clean motor wire routing.
        - Fixed motor slot circumference; motors will now fit nicely inside frame.
        - Fixed motor slot holes (for securing motors in place).
    - 3D printed CAD prototype.
- **Nick**:
    - Created first iteration of design document
    - Drew high-level drone design on lab whiteboard
    - Added circuit-design directory and uploaded first design
    - Started work on server communication
- **Parsa**:
    - Reviewed code on which protocol to use for GPIO communications
    - Talked and guided team to figure out our Problem, Need, and Goal statements
    - Looked and found a new ESC for the drone
    - Went to BELS to pickup Motor so we can test code with
- **Ryan**:
    - Research I2C vs SPI difference in drones
    - learned the basics of the PID for the motors
    - communication with Bels
    - started the PID code

## To-do, In-progress, Done:
- **To-do**:
    - Organize ESP code files
    - Work on the motor to esp connection
- **In-progress**:
    - PCB Prototype
    - Finalize CAD Design Prototype
    - CAD Dimensions
    - Finish up Problem, Need, and Goal statements
- **Done**:
    - 3D Print CAD Design Prototypes
    - Ordered Most parts

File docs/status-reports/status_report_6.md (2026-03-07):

# Status Report 6

## Achievements from before:
- Recieved a few parts
- Configured a viable test to demonstrate motor movement using a DC motor

## Setbacks from before:
- Motor pod sizing mismatch with motor that came in
- We did not receive our ESC which prevents us from connecting our brushless motor

## Who Did What:
- **Christian**:
    - Tested scripts on determining udp packet ports
    - Learning wireshark
    - Worked on design document
- **Kenny**:
    - Implemented a test to demonstrate the motor
    - Test includes speed and direction capabilities
    - Developed the wiring using a H-bridge and a potentiometer
    - Worked on design document
- **Kevin**:
    - Uploaded this week's meeting notes.
    - Redesigned high level schematic to not have images, added detail between parts, and overall look.
    - Added block diagram of schematic to the design document.
- **Matin**:
    - Updated our Notion Gantt Chart.
    - Fixed grammar and spelling errors on the design document via Overleaf (LaTeX).
    - Worked on design document with everyone.
    - 3D printed another drone frame.
- **Nick**:
    - Researched and uploaded notes for drone mesh network
    - Worked on Design Doc
        - Added content for Technology and Simulations
        - Updated parts list
    - Started research on wiring with Kenny
- **Parsa**:
    - Formatted design document to include all of the requirements
        - Fixed changes in design
        - Fixed Need and goal statements
        - Added appendices
    - Looked into parts for infared cameras that can be implemented
    - Researched esp-to-esp communication protocol to settup groundstation network
- **Ryan**:
    - ordered more parts
    - got the script to light up 2 udp packets
    - tried the wireshark

## To-do, In-progress, Done:
- **To-do**:
    - Waiting on remaining parts
- **In-progress**:
    - Presentation Slides
    - Design Document
- **Done**:
    - Hardware test for prototype demonstration

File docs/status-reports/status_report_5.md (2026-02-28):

# Status Report 5

## Achievements from before:
- changed the path of the project to something thats acheivable

## Setbacks from before:
- Still waiting for parts
- changed needs and goal states to something with purpose to fits our project better

## Who Did What:
- **Christian**:
    - Worked on Design Document
- **Kenny**:
    - Built a prototype of the motor and motor controller
    - Used an H-bridge found at BELS to link the ESP and the motor together
    - Wrote simple code to make the motor spin
- **Kevin**:
    - Converted white board drawing of high level design to digital format to be easily edited
    - Uploaded Feb_23_Notes.md covering focus on reworking Needs/Goal and prototype demonstrations
- **Matin**:
    - Made the drone-design-5 CAD volume larger to accommodate all the electronics going inside.
    - Placed all drone-design-5 files in its own subdirectory (for cleanliness).
    - Fixed the GitHub README.md to reflect the new need/goal statement of our project.
    - Cleaned up script_prototype.md.
    - Cleaned up FEB_23_NOTES.md.
- **Nick**:
    - Worked on Design Document
        - Reformatted to better fit requirements
        - Added need and goal statements
        - Added title page and executive summary
    - Started research on connecting between esps
- **Parsa**:
    - Set up SHTC3 sensor on the esp32-c3 to detect humidity and temp readings, should be able to convert that on to the new sensor thats coming.
    - Edited Design doc, added personas, Needs and Goal, and any existing reserach
    - cleaned up the github build files
- **Ryan**:
    - Researched controller app
    - wrote code to connect establish the wifi router on the esp
    - succesfully connected the esp to the app
    - submited new materials

## To-do, In-progress, Done:
- **To-do**:
    - Receive the parts
- **In-progress**:
    - Refining design documentation
- **Done**:
    - Circuit schematic
    - Needs and Goals finalized

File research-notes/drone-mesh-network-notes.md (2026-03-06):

1. Tooling and base Rust project
Install prerequisites:
Rust (nightly), cargo-generate, ldproxy.
ESP‑IDF (Espressif’s SDK) with C toolchain for ESP32‑C3.
Create a new Rust + ESP‑IDF project:
Use esp-idf-template or similar starter: cargo generate esp-rs/esp-idf-template.
Configure the target for ESP32‑C3 (e.g., riscv32imc-esp-espidf) per the rustc ESP‑IDF docs.
Flash a blink or Wi‑Fi example to confirm pipeline (build → flash → serial monitor) works for one DevKit‑RUST board.

2. Decide roles: root vs. normal nodes
Pick one node to be the root/gateway
Join the mesh as the root.
Also connect to base network (Wi‑Fi AP) or a modem.
Run an HTTP/HTTPS or MQTT client to report alerts to server.
All other nodes are leaf/router nodes:
They only join the mesh and forward sensor alerts toward the root.
Build one firmware with a ROLE_ROOT compile‑time flag or runtime config (e.g., GPIO strap, NVS flag) to switch behavior.

3. Bring up Wi‑Fi + mesh in Rust
Call the ESP‑WIFI‑MESH C APIs through Rust’s ESP‑IDF bindings.
Ensure esp-idf-sys is enabled so ESP‑IDF components (Wi‑Fi, mesh) are compiled in.
In main, do the standard ESP‑IDF init from Rust:
Initialize NVS, event loop, and Wi‑Fi: mirror the ESP‑MESH “event initialization” and “Wi‑Fi initialization” snippets.
Initialize the mesh:
Call esp_mesh_init() via FFI.
Register a mesh event handler (MESH_EVENT) to track when the node attaches, gets a parent, becomes root, etc.
Configure mesh parameters:
Set mesh ID (a shared 6‑byte ID).
Configure channel, router SSID/pass (for the root), and max layer/depth as in the ESP‑MESH guide.
Start the mesh:
Call esp_mesh_start() and wait for mesh events indicating the node is connected before sending/receiving packets.
At this point every board, when powered, should auto‑organize into a mesh—no external router required.

4. Design the fire‑alert message format
Define a tiny struct for messages, e.g.:
Node ID (u16).
Timestamp or sequence number (u32).
Fire risk level (0–255).
Optional sensor summary.
Serialize to a fixed‑size byte array (e.g., with bytemuck or a hand‑rolled layout) so it can send it directly over mesh packets.
Add a hop limit/TTL byte in the header so forwarded messages eventually expire and don’t loop forever.

5. Sending and receiving over ESP‑MESH
On every node (Rust side calling C APIs):
Receiving task:
Create a dedicated task (thread) that calls esp_mesh_recv() in a loop and pushes received packets into a Rust channel/queue.
Parse the header, decrement TTL, drop if expired.
If this node is the root and the message is an alert, enqueue it for server upload.
Sending function:
Wrap esp_mesh_send() in a safe Rust function that takes message struct and a destination:
For “send toward base”: use MESH_ROOT as destination, so the mesh routes it upward.
Forwarding logic:
Non‑root nodes: whenever they receive a packet addressed to the root (not them) and TTL > 0, re‑send it upward.
Root node: process and do not forward further.
The official programming guide shows typical esp_mesh_send/esp_mesh_recv usage and typical buffer sizes.

6. Sensor reading + alert logic
Use the DevKit‑RUST I2C mapping (SDA/SCL pins and addresses) to talk to built‑in sensors like SHTC3 and IMU.
In Rust:
Initialize I2C using esp-idf-hal and attach suitable drivers (e.g., shtcx, icm42670) as shown in the Rust ESP board examples.
Periodically read temperature, humidity, maybe motion or other fire‑relevant data.
Define a simple risk algorithm for now:
If temperature > threshold and humidity < threshold → raise risk.
Optionally include rate of change for early detection.
When risk exceeds some level, create an alert message and send it toward the root via esp_mesh_send().

7. Root node to base server (HTTPS/MQTT)
On the root firmware:
In the mesh receive task, when you get a valid alert:
Push it into another queue for the “uplink” task.
Uplink task:
Use esp-idf-svc’s HTTP or MQTT client implementations to connect to  server over Wi‑Fi.
For HTTPS, enable TLS in the client config (CA bundle, server name, etc.).
Send alert data as JSON or a compact binary frame to base server endpoint.
Handle reconnection:
If Wi‑Fi uplink is down, buffer a small number of alerts in RAM or flash, and retry periodically.

8. Deployment and tuning for the forest
Field test a line of 3–5 nodes:
Verify multi‑hop delivery and measure typical RSSI and latency.
Adjust spacing until reliable links.
Mesh parameters:
Tune maximum layers (mesh depth) and node density to match forest geometry.
If needed, enable Wi‑Fi long‑range mode on links with weak RSSI.
Power strategy:
Add periodic sleep/wake if battery constrained (e.g., wake every N seconds, read sensors, send if alert, then sleep).
May need to mix ESP‑MESH with Wi‑Fi power‑save options; start with always‑on for simplicity, then optimize.

9. What to code first
One board: Rust project that connects to Wi‑Fi AP and prints IP over serial.
Same board: add I2C sensor reading and log temperature/humidity.
Two boards: port the ESP‑MESH init/start/send/recv calls and confirm we can send a string between them.
Many boards: swap the string for alert struct and add forwarding and TTL.
Root board: add HTTP/HTTPS client to POST received alerts to a local Flask/Express test server.

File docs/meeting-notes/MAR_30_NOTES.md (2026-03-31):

# Notes

## Class Themes
- Working as a team
  - Communication
  - Contribution %
- Sizing / Complexity
  - Make sure everyone is busy
- Testing
  - Test plan (manufactured product)
  - Test results (prototype)
  - Automated tests (code)

## Deliverables
- Design document (by Week 8)
- Functional prototype
- Poster
- Presentation (Week 10)

## Schedule
- Week 1
  - Office hours on Zoom (need 2 members)
- Week 2-5
  - Instructor: Every other week, 30 mins, lecture
  - TA: Every other week, 30 mins, lab
  - Friday: Office hours
- Week 6-7
  - Instructor: 15 mins, Zoom, every week
  - TA: 30 every other
  - Posters: May 13, Wed
  - Friday: Office hours
- Week 8
  - Final prototype: MWF in lab
  - Senior Design Showcase: Thu May 21
- Week 9
  - Individual interview, 4 mins each, on Zoom
- Week 10
  - Presentations: MWF

## Tasks
- Kanban boards
- Create script to show repo contributions
  - Git log against up-to-date clone
  - Ignore bulk loaded data
  - Concentrate on code, documentation, etc.

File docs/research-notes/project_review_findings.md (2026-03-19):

# Project Review Findings

Date: 2026-03-18

Scope reviewed:
- Active embedded firmware in `main/scripts/**` and `main/testing/motor/**`
- Base-station and telemetry code in `main/base-server/**`
- Build and configuration surfaces at the repo root and in reference projects

## Findings

### Critical

1. The motor-control path accepts unauthenticated and unbounded ESP-NOW commands.
   - `main/scripts/ESPNowEasy.cpp:75` accepts any packet with `len >= sizeof(MessageType)`.
   - `main/scripts/MotorReceiver.cpp:96` ignores `src_mac` instead of validating it against `remote_mac`.
   - `main/scripts/MotorReceiver.cpp:101` through `main/scripts/MotorReceiver.cpp:116` compute and apply PWM duty without clamping.
   - `main/testing/motor/main/motor.c:105` through `main/testing/motor/main/motor.c:107` already show the safer clamped behavior in the test firmware.
   - Impact: any same-channel ESP-NOW sender can inject a 4-byte payload and command the motor; malformed values can push invalid LEDC duty values.

### High

2. The repo-root ESP-IDF build does not include the actual drone receiver or motor firmware.
   - `main/CMakeLists.txt:1` only registers `scripts/RemoteSender.cpp` and `scripts/ESPNowEasy.cpp`.
   - `main/scripts/MotorReceiver.cpp:120` contains a separate `app_main`, but it is not part of the root build.
   - Impact: the default firmware build path produces the controller-side prototype only, not the motor-side receiver.

3. The ESP-NOW bridge and the Rust ground-station server are disconnected.
   - `main/base-server/espnow_drone_base_server/main/fire_bridge.c:20` only receives packets and pretty-prints them to UART.
   - `main/base-server/espnow_drone_base_server/main/fire_bridge.c:106` starts the bridge loop with no forwarding behavior.
   - `main/base-server/fire-server/src/main.rs:181` starts a separate TCP server on `0.0.0.0:7878`.
   - Impact: the in-repo drone -> bridge -> server telemetry path is not implemented end-to-end.

4. The Rust server assumes a complete request arrives in a single TCP `read()`.
   - `main/base-server/fire-server/src/main.rs:117` through `main/base-server/fire-server/src/main.rs:125` read once into a fixed buffer.
   - `main/base-server/fire-server/src/main.rs:150` immediately treats the second parsed line as complete telemetry.
   - Impact: valid fragmented TCP requests can be rejected with `400 FAIL` or parsed as partial data.

5. The Rust server creates an unbounded blocking thread per connection with no timeout.
   - `main/base-server/fire-server/src/main.rs:119` blocks on `stream.read()`.
   - `main/base-server/fire-server/src/main.rs:185` through `main/base-server/fire-server/src/main.rs:188` spawn a new thread for every incoming connection.
   - Impact: idle or abusive clients can pin threads indefinitely and exhaust server resources.

6. The Rust project files are lowercase, which breaks Cargo on case-sensitive filesystems.
   - `main/base-server/fire-server/cargo.toml:1` should be `Cargo.toml`.
   - `main/base-server/fire-server/cargo.lock:1` should be `Cargo.lock`.
   - `main/base-server/README.md:6` through `main/base-server/README.md:8` instruct users to run Cargo there.
   - Impact: this may appear fine on a default macOS checkout, then fail on Linux or any case-sensitive filesystem.

7. The top-level ESP-IDF project hard-requires `IDF_PATH` even though the repo README claims there is a local ESP-IDF checkout.
   - `CMakeLists.txt:3` includes `project.cmake` only from `$ENV{IDF_PATH}`.
   - `README.md:26` says the repo contains `esp/esp-idf/`.
   - Impact: a fresh checkout with only the documented local tree still will not configure unless `IDF_PATH` is manually exported.

8. The ESP-NOW base-station link is fragile because it depends on hard-coded board identity and implicit channel selection.
   - `main/base-server/espnow_drone_sender/main/fire_drone.c:18` hard-codes the bridge MAC address.
   - `main/base-server/espnow_drone_sender/main/fire_drone.c:153` through `main/base-server/espnow_drone_sender/main/fire_drone.c:156` add the peer with `channel = 0`.
   - `main/base-server/espnow_drone_base_server/main/fire_bridge.c:91` starts Wi-Fi but does not pin an explicit channel.
   - Impact: swapping boards or drifting off the implicit channel can silently break delivery with no recovery flow.

### Medium

9. `DroneReceive.cpp` is out of sync with the active ESP-NOW wrapper and will not compile if it is added back to a build.
   - `main/scripts/ESPNowEasy.h:14` defines `ReceiverCallback` as `(MessageType&, const uint8_t*)`.
   - `main/scripts/DroneReceive.cpp:12` still defines `handleIncoming(Message&)`.
   - `main/scripts/DroneReceive.cpp:24` passes that outdated callback signature into `onReceive`.
   - Impact: the file is stale and masked only because the root build currently excludes it.

10. `fire_drone.c` ignores the SHTC3 CRC bytes.
   - `main/base-server/espnow_drone_sender/main/fire_drone.c:86` reads the full 6-byte SHTC3 frame.
   - `main/base-server/espnow_drone_sender/main/fire_drone.c:100` through `main/base-server/espnow_drone_sender/main/fire_drone.c:105` convert raw values without validating `data[2]` or `data[5]`.
   - Impact: I2C bus corruption can become believable but incorrect telemetry.

11. The repo contains a stale parallel `ESPNowEasy` implementation and reference project with no guardrails.
   - `main/scripts/ESPNowEasy.h:14` uses the active two-argument callback API.
   - `main/lab4_1/main/ESPNowEasy.h:15` still uses the older one-argument callback API.
   - `main/lab4_1/CMakeLists.txt:6` keeps that tree as a standalone ESP-IDF project.
   - `main/lab4_1/README.md:4` shows it is an unrelated stock I2C example.
   - Impact: it is easy to edit or build the wrong tree and follow misleading instructions.

## Review Notes

- This review was source-based and validated across multiple project areas.

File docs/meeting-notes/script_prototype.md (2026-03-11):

# Prototype Demonstration Script (Mar. 10 Revision)

## Total Time
- Target length: 15 minutes
- Q&A: 5 minutes
- Main visual for most of the demo: `circuit-design/Schematic_Design_2.png`
- Required flow:
  - Need/Goal
  - Design Objectives
  - Personas
  - Testing Plan
  - The Design

## Opening (Need + Goal)
"Hi everyone, we are Team FireFly.

The need we are addressing is that remote and high fire-risk areas often do not have fixed sensor infrastructure during the critical pre-fire window. Because of that, fire response teams can be left without timely environmental data when they need it most.

Our goal is to provide a rapidly deployable monitoring system that can gather temperature, humidity, and smoke information in infrastructure-free terrain and return that information to operators so they can make earlier and safer decisions.

For this prototype demonstration, we are showing that the core communication and control architecture can be tested in modular pieces and still map directly back to that need and goal." 

## Personas
"This design is meant for users across a wide experience range.

One example user is a wildfire operations coordinator who needs a system that is fast to deploy, easy to understand, and reliable under time pressure.
Another example is a researcher who wants environmental data collected in remote areas and forwarded into a computer-based workflow for logging and analysis.

Mentioning personas is important because it explains why our design emphasizes clear operation, practical deployment, and a simple data path instead of extra features that do not help the user in the field." 

## Design Objectives
"Our design objectives are measurable, because we need a way to decide whether the design actually meets expectations.

First, the system needs enough transmission range to operate away from the operator in realistic outdoor conditions.
Second, the transmission rate needs to be fast enough that commands and environmental readings stay useful.
Third, battery life needs to support a meaningful monitoring mission, not just a very short bench test.
Fourth, the system needs to operate across the temperature conditions expected in wildfire monitoring environments.

These objectives matter because they turn the project from an idea into something we can test numerically and improve with evidence." 

## The Design
"Using the schematic, we can connect that prototype back to the full design.

On the left side is the power and actuation path: the battery, the electronic speed controller, the motors, and the propellers.
At the center is the controller (MCU), which acts as the decision point for sensing, communication, and control.
On the right side is the operator path: a computer connects by USB to a ground-station controller, and the computer can also connect to a server for logging and monitoring.

In the final system, environmental readings would move from the sensors into the drone controller, across the wireless link, and back to the ground side for display and storage. In today's prototype, we use a command packet from a microcontroller and another microcontroller to control a motor." 

## Testing Plan + Prototype Evidence
"Our testing plan is to validate one functional part of the high-level design at a time.

For today's prototype, we focus on the communication path. A computer sends a counter over USB to the ground-station controller. That message is transmitted over the wireless link to the controller. The controller responds by updating a counter received .

That Counter is the visible proof in this demo. It shows that a message traveled across the intended link and triggered a response on the receiving side.

## Close
"To close, this prototype demonstrates five things.

First, the project is grounded in a clear need and goal.
Second, the design is being judged against measurable objectives.
Third, the system is being shaped around real users and real field constraints.
Fourth, our testing plan is evidence-based.
Fifth, the prototype result supports the overall design by proving that the communication path can produce a successful response.

Our next step is to extend that validated path into the rest of the system, including integrated sensing, motor control, and broader end-to-end testing." 

## Presenter Notes
- Keep the Need and Goal statement strong and memorized.
- Do not frame the demo around a phone or app.
- Do not name the board model directly; say `ground-station controller`, `drone controller`, `MCU`, or `wireless link`.
- Emphasize that this is a prototype test of one functional subsystem, not the full final deployment.

## Backup One-Liners for Q&A
- "Why remove the phone/app stage?" -> "The revised schematic focuses on the computer, ground-station controller, and drone controller path so we can test the core wireless link more clearly and reduce demo risk. As well as setup One to many drones to send out communications commands to"
- "What does the blinking LED prove?" -> "It proves the remote node received the message and executed the expected action."
- "What is working today?" -> "The end-to-end path from computer to ground station, across the wireless link, to the drone-side hardware response is working in the current prototype test."
- "What are you proving today?" -> "We are proving the communication architecture and the testing approach, not full flight operation."

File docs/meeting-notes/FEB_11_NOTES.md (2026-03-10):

# Notes

## Sizing / Measurements
- Talked about wing to wing dimensions, so it would be 127mm by 127mm from each wing span
- Measured the esc module and where it would go in the box
- Talked about if its better strapping the battery on the bottom of the housing, and possibly adding landing mounts to protect battery from landing
- Also mentioned if we still need wing protectors, might add that in for next quarter

## Optimizing Modularity
- Implement pass through connectors to implement a receiver system where we can plug and play with sensor
- Using the pass through connectors we have permanent soldered pins so user can just plug sensor into the pass through connectors

## General
- got caught up on meeting with the professor
- Talked about the perforated board

## Concerns
- Timing on when the parts would arrive, if there's any delays we would need to communicated with BELS to get some sort of expedited shipping on the main materials we need

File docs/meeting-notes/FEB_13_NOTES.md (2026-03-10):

# Notes

## General
- Organize imported code files
- Meeting time next week on Thursday during class time at lab
- Catching up members on last meeting
- Finish status report

## CAD / Parts
- 3D print and design individual parts to test sizing issues
- Magnetic cover for case/ sliding lid
- Circuit Diagram

## Concerns
- Delivery time of parts (asap)
- Make personas

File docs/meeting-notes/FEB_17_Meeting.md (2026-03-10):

## High Level Design:

- **Microcontroller/ESC**
  - Ram  
  - CPUs  
- **Receiver**
  - App  
  - Wifi/BLE  
  - Logging actions from drone  
  - HTTP Server  
- **Audience**
  - How to make it educational  
  - Functional from $50 range to more  
  - Starter kit

- **Testing**:
  - Data received/logged  
  - Motor spinning

- **Prototype**:
  - Motors in frame with battery  
  - Testing connection from phone to ESP  
    - Move up → led lights up in up direction… etc  
  - Color grading for presentation  
  - Make a non-programmer program the drone  
    - Configure the drone in a way anyone can do it

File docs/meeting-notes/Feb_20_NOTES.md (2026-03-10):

# Notes

## Prototype vs High Level Design
- Make a small part of high level design functional, not full design
- Need and Goal Statement
- Not sufficient for a 123 Project?
- Audience Spectrum
  - Can google and code
  - Can't code
  - Make it specific
- Pricing
  - Open source then copy
  - Can be dodgy
- Not designing prototype
- Flying instructions
  - How high the drone is
  - Stationary flying
  - Flying 3 meters forward then back

## Need/Goal
- There can already be a product like our design
- What is the need ex:
  - Smart Vending Machine
  - Tells you what you buy and if it's healthy etc
- Fix this
- Build around need

## Prototype
- Implement some parts that work to showcase how to make high level
- Document meant for another team of engineers
- Functional parts
  - Send communication between devices
  - If one motor can spin from communication then proves for four
- Focus on the functional portions for now

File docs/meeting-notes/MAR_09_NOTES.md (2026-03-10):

# Notes

## Meeting Goals
- Testing goals

## Testing
- Design document / testing
  - "Sensors should work at range ... and outside at range ..."
  - 5 items
    - Need/Goal
    - Design objectives (02.01)
      - Measurable
      - Transmission range
      - Transmission rate
      - Battery life
      - Temperature range
    - Personas (02.02)
    - Testing plans
    - The design
- Numerical testing
- App testing
  - Able to connect app and ESP through computer's connection
  - Cut from design

## Changes
- Review design document
  - Need/Goal statement memorized
  - Remove live transmission
- Design
  - Remove phone/app
- Phone/App Stage -> Computer
  - Cut stage and directly from connect to a computer and server
  - Program commands like "Fly vertically 1 meter and hover"
  - Call functions to grab/curl data
- Testing
  - Communicate with ESP1 to ESP2 and have ESP2 have a flashing/blinking light
  - ESP-NOW
- Script
  - 15 mins + 5 mins of Q&A
  - Explain the 5 items
  - Don't need to answer all the questions

## Summary / Closing
- Server <- Computer -> ESP1 -> (ESP-NOW) -> ESP2 -> Blinking LED on ESP2
- Changed design from phone to computer via ESP-NOW
- Focus on Need/Goal
- No mention of ESP

## Design Objectives
- "Quantifiable expectations of performance" that you aim for, or try to achieve
- Identify performance characteristics that are of most interest to the client
- Describe those characteristics in a way "you and the client" can "decide" if the design meets expectations
- Describe the conditions under which a design will operate
- Example
  - Objective:
  - Design an inexpensive to manufacture battery carrier that does not reduce battery life, can be quickly replaced by Apple Store "Geniuses", and is cost-effectively recyclable

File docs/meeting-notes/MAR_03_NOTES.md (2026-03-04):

# Notes

## Instructor Meeting
- Current testing is too low level.

## Testing Improvements
- Force UDP packet drops and test reliability.
- Deliberately degrade the connection to simulate poor conditions.
- Check signal changes from voltage variation for testing.

## Sensor Requirements
- Define what the drone sensor needs to detect.
- Run independent tests.
- Evaluate other sensor types.
  - Infrared
- Determine whether we can detect a heat source.
- Determine whether we can locate where the heat source is.

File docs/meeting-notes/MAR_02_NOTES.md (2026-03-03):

# Notes

## Meeting Goals
- Some parts came in
- Review of demonstration

## Review of Last Week
- Sent packets to port on ESP but were unable to receive packets
- Got motor to spin
- Using ESP controller app is approved
- ESP-NOW: ground station sends data
  - Own protocol
- GPS vs Controller
- Leave out drone from need/goal

## Goals of The Week
- Communication between ESPs
- Design document
  - Finish up
- High-level design schematic
  - Clean up
  - "Blown up" section
  - Remove images
- Testing
  - Received signal text
  - Motor spinning log error
  - Wireshark

## Summary / Closing
- Do SETS
- Design document
- Schematic
- Script

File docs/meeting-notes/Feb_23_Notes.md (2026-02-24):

# Notes

## Meeting Goals
- Need/Goals
- Plans for Demo
- Make sure things are up to date for deadlines of quarter

## Need/Goal
- Wildfire Response Monitoring Drone
- Network Sensors vs Drone in areas without sensors
- Not in the format the prof wants
- Pre/Post Fires

## Testing
- Signal from phone to something
- Location sensing

## Objectives
- Get a signal sent from the phone to the esp
- Get a motor to spin from the esp32
- **Draft Design Document**
- Get something tangible for Instructor Meeting

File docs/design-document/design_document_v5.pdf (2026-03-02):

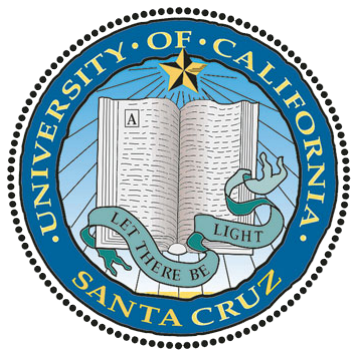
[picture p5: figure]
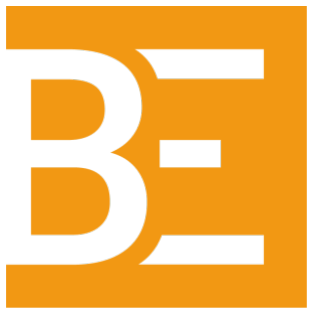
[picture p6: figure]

# FireFly Design Document

Christian Li, Kenny Wang, Kevin Yao, Matin Sobhani, Nick Lafredo, Parsa Rezvani, Ryan Yu

Contents

1 | Introduction | 4
2 | Design | 5
3 | Parts List | 7

Abstract

This document explains how to design, build, and operate the FireFly FireWatch Drone.

Index Terms

none

Executive Summary
FireFly is a rapidly deployable quadcopter platform designed as a first-response environmental monitoring tool for high wildfire-risk areas with little or no sensor infrastructure. The system integrates temperature, humidity, and smoke sensing with live data transmission to a ground station, enabling early awareness and alerts when fire-risk is detected. Its mechanical and electrical architecture allows it to adapt to different terrains and sensing requirements.
The design section of the document specifies system requirements for payload capacity, flight time, communication range, and sensor capability. It targets operation in terrain suited poorly for manual monitoring. The architecture defines the flight controller, power distribution, propulsion stack, communication link, and sensor bus. The mechanical design focuses on a 3D-printed frame with mounting points for motors, batteries, and payloads.
Power and propulsion modules are chosen to maximize flight time, while keeping a stable rate of power consumption. Sensor and payload modules include environmental sensors that measure temperature, humidity, and smoke concentration to support fire monitoring. The electronics and control subsection describes how the flight controller interfaces with ESC, receivers, and sensors over buses.
Safety and reliability are assured through design features and planned validation. Propeller guards and keyed connectors prevent user error and physical hazards. The document outlines bench testing for individual modules (power, propulsion, sensors, communications) and flight testing for stable hover, controlled movement, data link, and detection of smoke/temperature. These elements aim to demonstrate that FireFly can serve as a practical platform for wildfire monitoring and emergency response research.

### 1 Introduction

This document contains all the information needed to design and use the FireFly Drone.

Why is collecting data during a pre-fire window important? A pre-fire window—the period before an incident occurs—is critical because it provides time-sensitive information that improves responder safety, reduces property damage, and enables faster, more effective emergency response. Data on vegetation conditions, topography, temperature, humidity, and smoke concentration helps predict fire behavior, identify high-risk areas, and support mitigation actions such as controlled burns or targeted thinning operations. Without this information, emergency crews arrive with incomplete situational awareness and must gather critical details in real time under dangerous conditions.

For wildfire response specifically, the challenge is compounded by geography. High-risk areas are frequently roadless wilderness where permanent sensor infrastructure cannot be installed or maintained. Satellite imagery and aerial patrols provide coverage, but both suffer from response delays and gaps during the highest-risk windows. The result is a critical blind spot: the pre-fire period in remote terrain is precisely where early awareness matters most, yet it is the hardest environment in which to collect data.

FireFly addresses this gap directly. By deploying a sensor-equipped quadcopter into areas with zero existing infrastructure, FireFly enables real-time collection of temperature, humidity, and smoke data during the pre-fire window, transmitting live readings to a ground station and triggering alerts when fire risk thresholds are crossed. The platform is designed for rapid deployment by field crews without requiring extensive training or specialized support, transforming what would otherwise be a period of uncertainty into a structured, data-driven response.

### 1.1 Need Statement

A rapidly deployable drone that can be launched immediately into high fire-risk areas with zero sensor infrastructure, collecting real-time temperature, humidity, and smoke data during the high-risk window before a fire occurs.

### 1.2 Goal Statement

Prove that a drone can function as a first response, environmental monitoring tool by integrating a smoke and temperature sensor, transmitting live readings to a ground station, and triggering alerts when fire risk thresholds are crossed.

### 1.3 Personas

Individuals with experience levels ranging from novice to expert in fire monitoring and environmental fieldwork. End Users
Marcus
Role: Wildfire Operations Coordinator (professional first responder)
Background / Context: Works with a state forestry division managing prescribed burns and post-fire monitoring. Needs something fast that he can hand off to field crews without extensive training. Goals: Rapid deployment of sensor-equipped drones into areas too dangerous or inaccessible for personnel during the high-risk pre-fire window. Wants real-time smoke and temperature data without putting people in harm’s way.
Behaviors: Works under time pressure, values reliability over features, and coordinates with multiple agencies. Skeptical of unproven technology. Practical if it breaks in the field, it needs to be fixable on-site with minimal tools.
Expectations: A rugged, simple-to-operate platform that can be deployed at a moment’s notice. Wants clear threshold alerts he can act on immediately.

Elena
Role: Ecology Graduate Researcher (academic user)
Background / Context: Studying fire risk and ecosystem conditions at a land-grant university. Needs to collect environmental sensor data across wilderness areas where no permanent monitoring infrastructure exists. Currently hikes in with handheld sensors, which limits how often and how broadly she can sample.
Goals: Automate pre-fire data collection over defined survey areas. Wants live temperature,

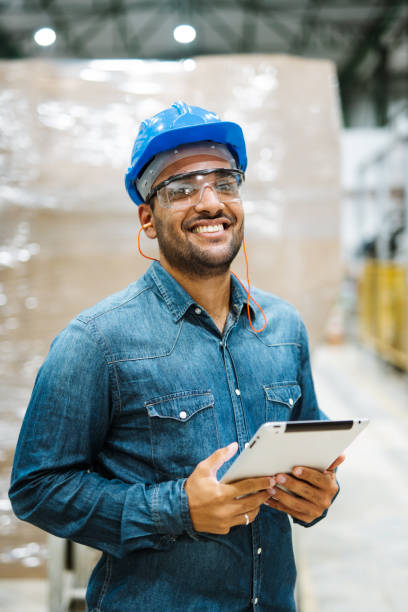
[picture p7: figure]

humidity, and smoke readings logged without requiring physical presence at each site.
Behaviors: Comfortable with technical documentation, participates in academic drone and environmental monitoring commu-nities, and documents everything for publication. Willing to configure and customize but does not have time to build from scratch.

Expectations: A reliable platform with a clear data pipeline she can connect to her existing research database, and results trustworthy enough to cite.

Experts / Consultants
Dr. Anita Rowe
Role: Environmental Sensor Systems Engineer
Background / Context: Works at a national lab developing atmospheric sensor arrays for wildfire monitoring. Has deep expertise in what data is actually actionable in pre-fire environments and where sensors fail under heat, humidity, and particulate exposure.
Goals: Validate that FireFly’s sensor suite captures meaningful data for fire risk assessment and identify unreliable component choices before they are locked into the design.
Behaviors: Data-driven and skeptical of consumer-grade sensors in harsh field conditions. Will probe calibration drift, operating temperature limits, and whether threshold alert logic reflects real-world fire risk indicators.
Expectations: A platform sound enough in its sensor selection and alert logic that field results can be trusted and the methodology can be defended to other scientists.

Client

U.S. Forest Service Regional Office
Role: Federal Land and Fire Management Agency
Background / Context: Responsible for fire prevention, monitoring, and response across millions of acres of national forest, much of it roadless wilderness with no existing sensor infrastructure. Currently relies on satellite imagery, fire lookout towers, and aerial patrols, all of which have coverage gaps and response delays during the highest-risk windows.
Goals: Evaluate FireFly as a rapidly deployable supplement to existing monitoring systems for areas where infrastructure cannot operate. Interested in whether the platform can reliably trigger alerts before a fire establishes.
Behaviors: Evaluates tools based on operational reliability and ease of use for non-specialist field crews. Requires demonstrated performance data before recommending adoption.

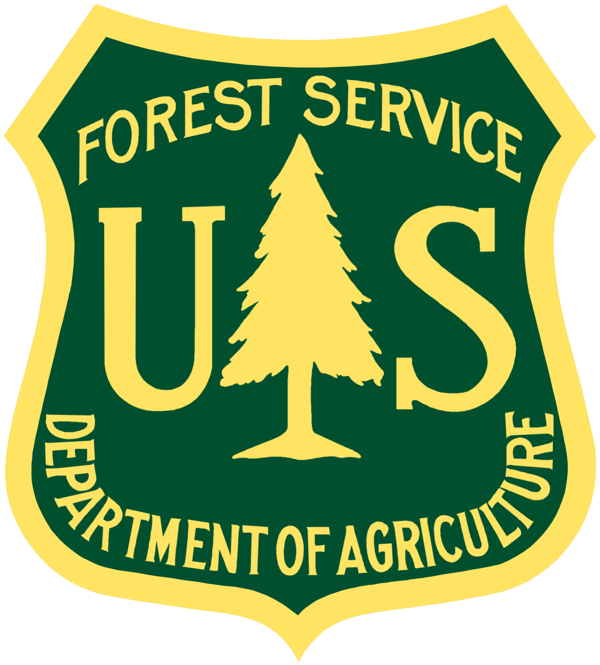
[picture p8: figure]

Expectations: A working prototype that proves the core concept, zero-infrastructure deployment, live sensor transmission, and threshold-based alerting, with documentation clear enough for field personnel to operate without engineering support.

### 1.4 Existing Research

Drone-based wildfire monitoring is an active research area, yet a clear gap remains for rapidly deployable, infrastructure-independent platforms targeting the pre-fire window in remote terrain.
Current detection methods rely on satellite imagery, fixed camera-tower networks, and manned aircraft. Satellites cannot reliably detect fires smaller than approximately 18 square kilometers, which limits early-stage intervention. Fixed towers such as AlertCalifornia’s 1,000-camera network are constrained by line of sight, leaving roadless and mountainous terrain uncovered. Research shows UAVs can bridge these gaps; for example, studies have demonstrated UAV–IoT networks detecting fires as small as 2.5 square kilometers with greater than 99 percent accuracy. However, many existing platforms depend on pre-deployed ground sensors, persistent connectivity infrastructure, or large multi-drone fleets, creating a blind spot in remote areas where such infrastructure is impractical.
FireFly targets the specific gap the literature acknowledges but has not fully addressed: a self-contained quadcopter requiring no pre-existing infrastructure, no persistent network, and no specialized operator training to deliver real-time environmental sensor data and threshold-based fire risk alerts.

### 1.5 Sustainability Statement

### 2 Design

### 2.1 System Requirements

[functional requirements.]
[payload, flight time, range, sensor capabilities.]

### 2.2 System Architecture

[overall block diagram.]
[flight controller, power, propulsion, communication, sensor bus.]

### 2.3 Mechanical Design

[frame layout and mounting points for motor, battery, ...]

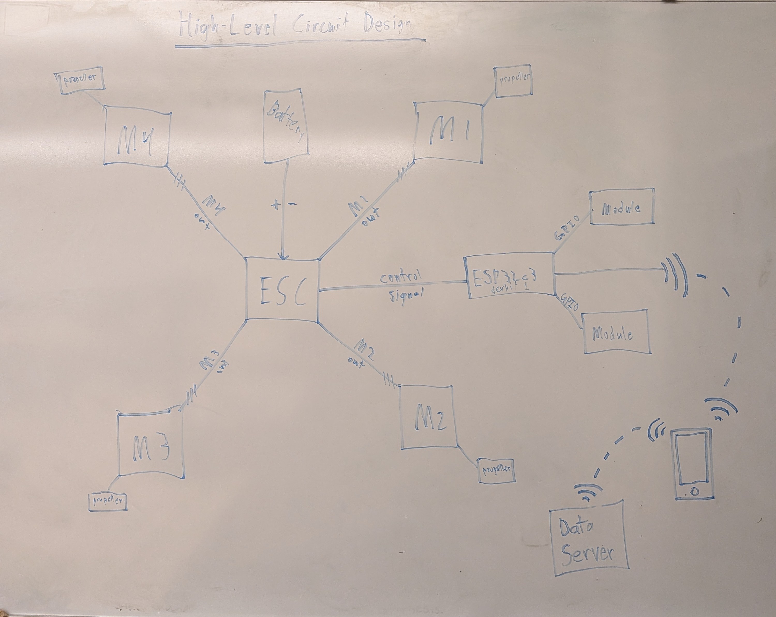
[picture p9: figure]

Fig. 1: A circuit diagram of the connections within our drone.

### 2.4 Power and Propulsion Modules

Our design uses a 4-motor propulsion system with a high KV rating, giving the drone the thrust and responsiveness needed to handle a wider range of operating conditions. The higher KV motors help the platform maintain stable flight so onboard sensors can take accurate readings. For power, we use LiPo batteries because they provide high energy density while keeping the package compact. A smaller, lighter battery reduces overall weight, which lowers the load on the motors and helps extend flight time.

### 2.5 Sensor and Payload Modules

[information about supported sensors (LiDAR, camera, ...), maximum excess payload, etc.]

### 2.6 Electronics and Control

[how to control the drone, what is needed for control, etc.]

### 2.7 Safety and Reliability

[testing logs and proof that it can take damage and handle failures.]
[physical safety information: prop guards, connector keying to avoid misplugging.]

### 2.8 Testing and Validation

[bench tests for each module.]
[flight tests and criteria.]

### 3 Parts List

Part | Set | Supplier | Quantity
CarbonX PLA+CF Filament | A | Creality | 1
Battery: LiPo 850 mAh 3S 25/30C | A | HobbyKing | 1
Motor: SunnySky R1106 FPV Brushless Motors | A | Druav | 4
Propeller: Gemfan Hurricane 2009-3 Tri-Blade (Set of 4) | A | Pyrodrone | 1
Battery: 3S 1000 mAh | B | HobbyKing | 1
Motor: RCINPOWER GTS 1204 5000KV | B | Pyrodrone | 4
Propeller: HQProp T3.5x2x3 | B | GetFPV | 1
Caddx Ant Lite Analog Camera (FPV Cycle Edition) | A / B | CaddxFPV | 1
TFMini-S Micro LiDAR Module | A / B | SparkFun | 1
HAKRC 20A 4-in-1 3-6S BLHeli_32 5V 3A BEC DShot1200 Mini ESC | A / B | Alibaba | 1
Perforated Circuit Board | A / B | Adafruit | 2
Female Header Pins 2x6 | A / B | AliExpress | 4
Female Header Pins 2x8 | A / B | AliExpress | 2
Female Header Pins 2x10 | A / B | Mikroe | 2

TABLE I: Itemized Budget

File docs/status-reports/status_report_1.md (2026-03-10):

# Status Report 1

## Achievements:
- We set up **Notion** accounts and are currently using it for **brainstorming** and a **Gantt chart**.  
- Made a **Discord server** and **iMessage/RCS** group chat with all 7 of us.  
- Made a **Google Sheets** tracking the cost of the parts we need.  
- Made a **Google Doc** to jot down project goals; includes our **need/problem/goal** statement.  
- We spoke with our TA on Monday as a group and got feedback/instructions.  
- We figured out our schedule concerning when we’ll all meet to work on the project. Also agreed on times for TA and Instructor meetings.

## Setbacks:
- Getting a SolidWorks key from BELS (we may use **Onshape** instead).

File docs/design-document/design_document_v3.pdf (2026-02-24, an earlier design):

# SpectreFLY Design Document

Christian Li, Kenny Wang, Kevin Yao, Matin Sobhani, Nick Lafredo, Parsa Rezvani, Ryan Yu

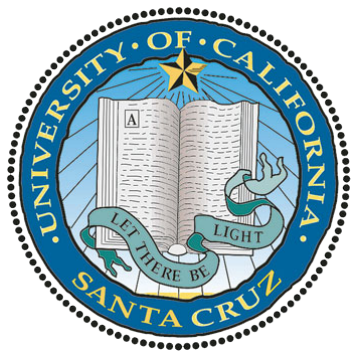
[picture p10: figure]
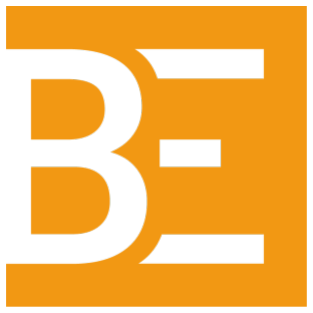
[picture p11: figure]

Contents

1 | Introduction | 3
2 | Design | 3
3 | Parts List | 4

Abstract—This document aims to teach the reader how to create the SpectreFLY FireWatch Drone.
Index Terms—none

Executive Summary
SpectreFLY is a rapidly deployable quadcopter platform designed as a first-response environmental monitoring tool for high wildfire-risk areas with little or no sensor infrastructure. The system integrates temperature, humidity, and smoke sensing with live data transmission to a ground station, enabling early awareness and alerts when fire-risk is detected. Its mechanical and electrical architecture allows it to adapt to different terrains and sensing requirements.
The design section of the document specifies system requirements for payload capacity, flight time, communication range, and sensor capability. It targets operation in terrain suited poorly for manual monitoring. The architecture defines the flight controller, power distribution, propulsion stack, communication link, and sensor bus. The mechanical design focuses on a 3D-printed frame with mounting points for motors, batteries, and payloads.
Power and propulsion modules are chosen to maximize flight time, while keeping a stable rate of power consumption. Sensor and payload modules include environmental sensors that measure temperature, humidity, and smoke concentration to support fire monitoring. The electronics and control subsection describes how the flight controller interfaces with ESC, receivers, and sensors over buses.
Safety and reliability are assured through design features and planned validation. Propeller guards and keyed connectors prevent user error and physical hazards. The document outlines bench testing for individual modules (power, propulsion, sensors, communications) and flight testing for stable hover, controlled movement, data link, and detection of smoke/temperature. These elements aim to demonstrate that SpectreFLY can serve as a practical platform for wildfire monitoring and emergency response research.

### 1 Introduction

This document contains all the information needed to design and use the SpectreFLY Modular Drone. [more later]

### 1.1 Need Statement

A rapidly deployable drone that can be launched immediately into areas with zero sensor infrastructure, collecting real-time temperature, humidity, and smoke data during the high-risk window before a fire occurs.

### 1.2 Goal Statement

Prove that a drone can function as a first response, environmental monitoring tool by integrating a smoke and temperature sensor, transmitting live readings to a ground station, and triggering alerts when fire risk thresholds are crossed.

### 1.3 Personas

### 1.4 Existing Research

Currently little to no versatile, quickly deployable solution to monitoring wildfires in areas without extensive fire monitoring.

### 1.5 Sustainability Statement

### 2 Design

### 2.1 System Requirements

[functional requirements.]
[payload, flight time, range, sensor capabilities.]

### 2.2 System Architecture

[overall block diagram.]
[flight controller, power, propulsion, communication, sensor bus.]

### 2.3 Mechanical Design

[frame layout and mounting points for motor, battery, ...]

### 2.4 Power and Propulsion Modules

[information about motors/propellers.]

### 2.5 Sensor and Payload Modules

[information about supported sensors (LiDAR, camera, ...), maximum excess payload, etc.]

### 2.6 Electronics and Control

[how to control the drone, what is needed for control, etc.]

### 2.7 Safety and Reliability

[testing logs and proof that it can take damage and handle failures.]
[physical safety information: prop guards, connector keying to avoid misplugging.]

### 2.8 Testing and Validation

[bench tests for each module.] [flight tests and criteria.]

### 3 Parts List

Part | Set | Supplier | Quantity
CarbonX PLA+CF Filament | A | Creality | 1
Battery: LiPo 850 mAh 3S 25/30C | A | HobbyKing | 1
Motor: SunnySky R1106 FPV Brushless Motors | A | Druav | 4
Propeller: Gemfan Hurricane 2009-3 Tri-Blade (Set of 4) | A | Pyrodrone | 1
Battery: 3S 1000 mAh | B | HobbyKing | 1
Motor: RCINPOWER GTS 1204 5000KV | B | Pyrodrone | 4
Propeller: HQProp T3.5x2x3 | B | GetFPV | 1
Caddx Ant Lite Analog Camera (FPV Cycle Edition) | A / B | CaddxFPV | 1
TFMini-S Micro LiDAR Module | A / B | SparkFun | 1
HAKRC 20A 4-in-1 3-6S BLHeli_32 5V 3A BEC DShot1200 Mini ESC | A / B | Alibaba | 1
Perforated Circuit Board | A / B | Adafruit | 2
Female Header Pins 2x6 | A / B | AliExpress | 4
Female Header Pins 2x8 | A / B | AliExpress | 2
Female Header Pins 2x10 | A / B | Mikroe | 2

TABLE I: Itemized Budget

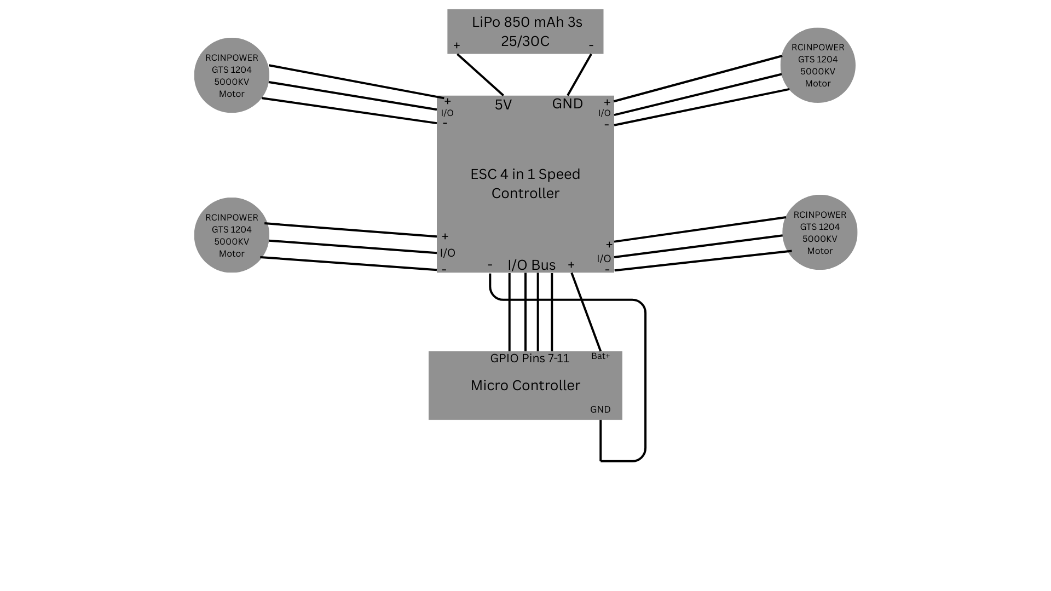
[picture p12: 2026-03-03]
docs/circuit-design/Circuit_Diagram.png

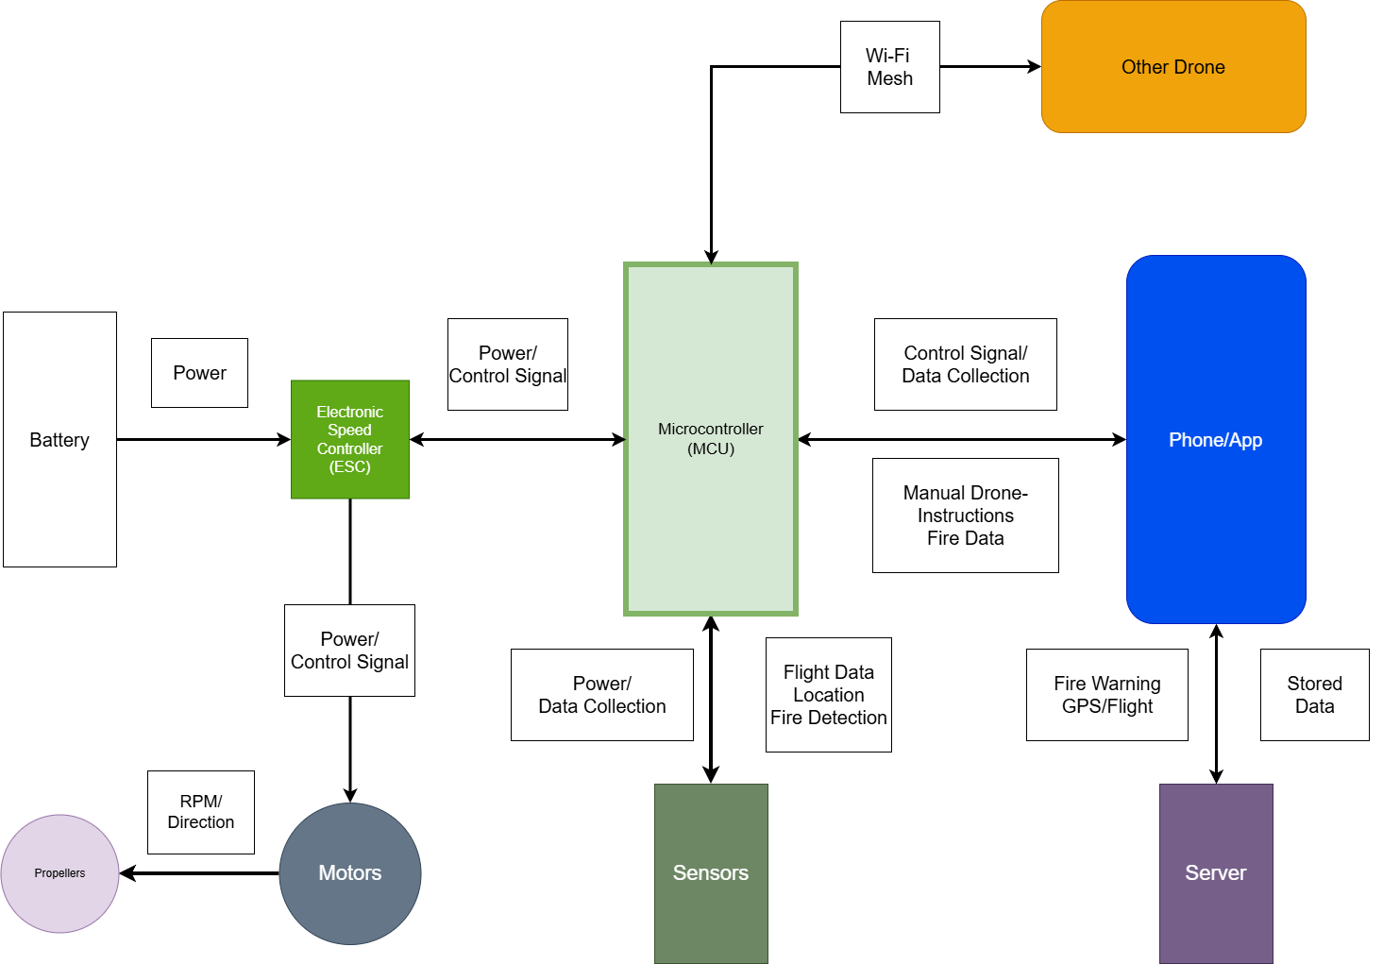
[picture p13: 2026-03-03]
docs/circuit-design/Schematic_Design.png

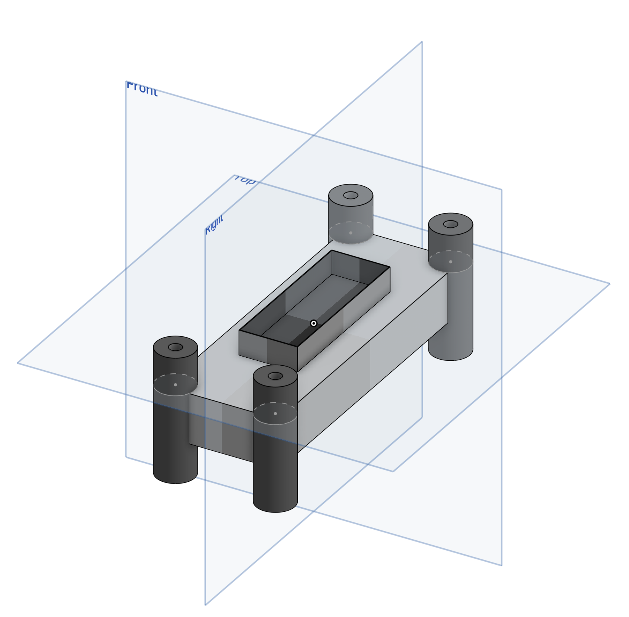
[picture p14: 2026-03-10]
docs/drone-designs/drone_design_2.png

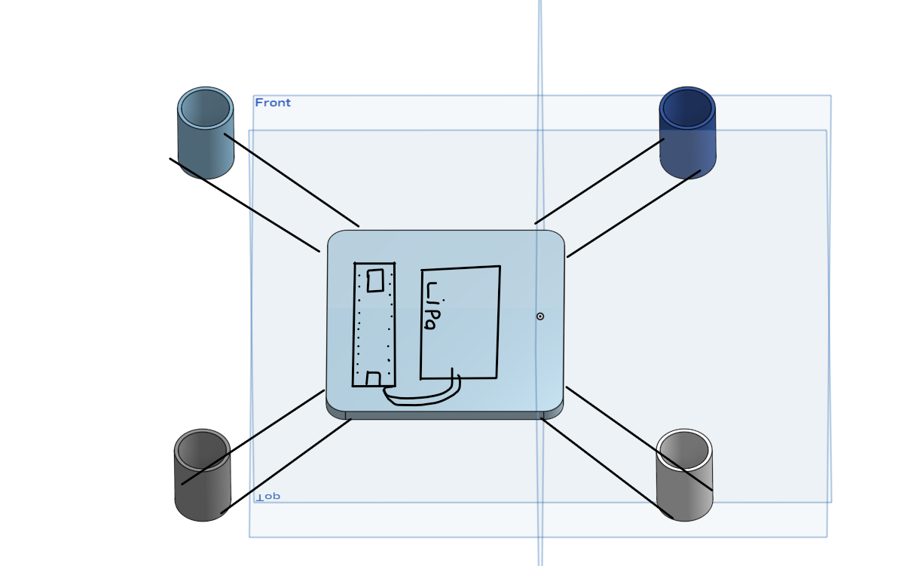
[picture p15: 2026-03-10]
docs/drone-designs/drone_design_4.png

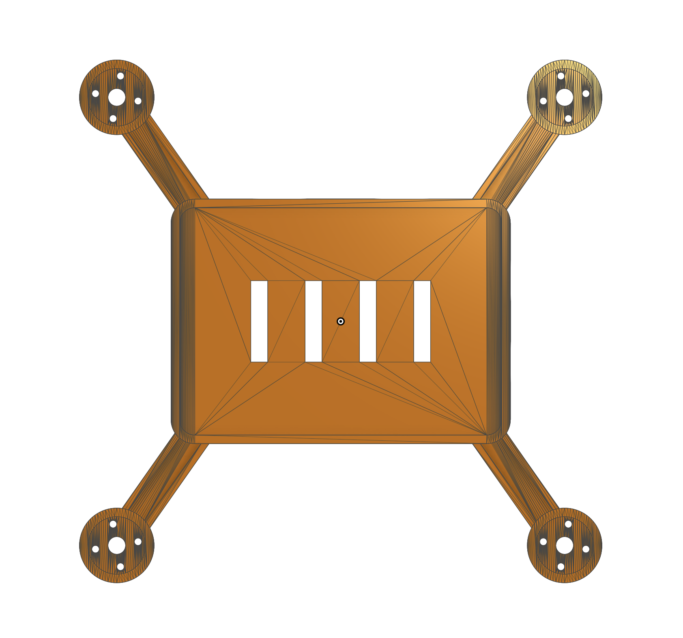
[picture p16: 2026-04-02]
docs/drone-designs/drone-design-5/option-b/drone_design_5_top.png

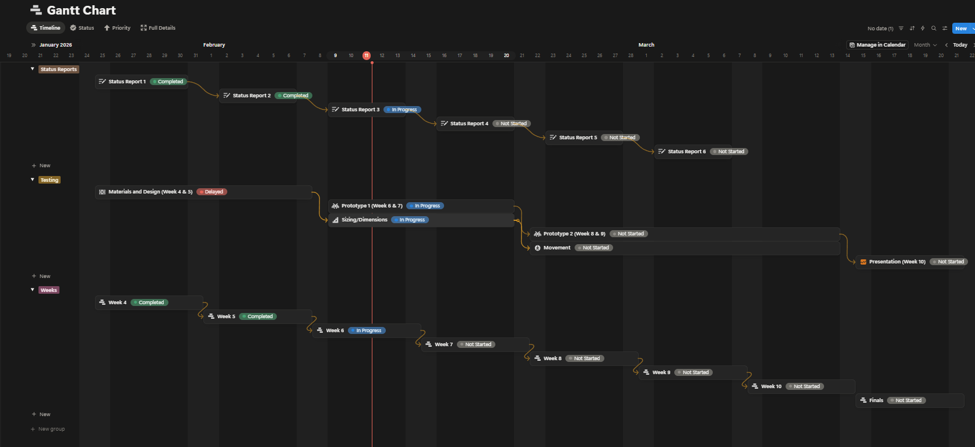
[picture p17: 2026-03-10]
docs/status-reports/Gantt_Chart_v1.png

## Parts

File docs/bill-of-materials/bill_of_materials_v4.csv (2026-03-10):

Item | Purpose | Price | Set | Quantity | Total | Link | Status
Battery: LiPo 850 mAh 3s 25/30C | 3 cells Lipo battery option 1 | $6.18 | A | 1 | $6.18 | https://hobbyking.com/en_us/turnigy-nano-tech-850mah-3s-25-40c-lipo-pack.html?wrh_pdp=2&countrycode=US
Motor: SunnySky R1106 FPV Brushless Motors | Brushless motors compatible with option 1 batteries for the propellors | $11.99 | A | 4 | $47.96 | https://druav.com/products/sunnysky-r1106-fpv-motors
Propeller: Gemfan Hurricane 2009-3 Tri-Blade | 4 sets of Tri-blade propellors compatible with option 1 motors | $4.99 | A | 1 | $4.99 | https://pyrodrone.com/products/gemfan-2512-2-5inch-3-blade-1-5mm-2mm-hole-propeller-4cw-4ccw
Battery: 3S 1000 mAh | 3 cells Lipo battery option 2, back up if the first set does not work | $10.99 | B | 1 | $10.99 | https://hobbyking.com/en_us/turnigy-1000mah-3s-40c-lipo-pack-jst.html?wrh_pdp=2&countrycode=US
Motor: RCINPOWER GTS 1204 5000KV Motor | Brushless motors compatible with option 2 batteries for the propellors | $18.99 | B | 4 | $75.96 | https://pyrodrone.com/products/rcinpower-gts-1204-5000kv-motor-choose-color
Propeller: HQProp T3.5x2x3 Propeller | 4 sets of Tri-blade propellors compatible with option 2 motors | $3.99 | B | 1 | $3.99 | https://www.getfpv.com/hqprop-3520-3-blade-1-5mm-shaft-propeller-set-of-4-grey.html
CADDXFPV Ant Lite Analog Camera (FPV Cycle Edition) | Add-on Camera to test modularity | $15.90 |  | 1 | $15.90 | https://www.caddxfpv.com/products/caddxfpv-ant-lite-4-3-fpvcycle-edition
TFMini-S - Micro LiDAR Module | Add-on sensor to test modularity | $72.95 |  | 1 | $72.95 | https://www.sparkfun.com/tfmini-s-micro-lidar-module.html
HAKRC 20A 4In1 3-6S Blheli_32 5V 3A BEC Dshot1200 Mini Size ESC | Electronic speed controller with a power regulator | $30.12 |  | 1 | $30.12 | https://www.alibaba.com/product-detail/HAKRC-15A-20A-30A-40A-4In1_1600358245493.html
Perforated Circuit Board | Building stack and connecting parts together | $4.95 |  | 2 | $9.90 | https://www.adafruit.com/product/2670 | Picked up from BELS
Female Header Pins 2x8 | Building stack and connecting parts together | $0.09 |  | 2 | $0.18 | https://www.aliexpress.com/item/2251832418097093.html?_randl_currency=USD&_randl_shipto=US&src=google | Picked up from BELS
Female Header Pins 2x6 | Building stack and connecting parts together | $0.17 |  | 4 | $0.68 | https://www.ebay.com/itm/400985399809?chn=ps&google_free_listing_action=view_item | Picked up from BELS
Female Header Pins 2x10 | Building stack and connecting parts together | $0.72 |  | 2 | $1.44 | https://www.mikroe.com/2x10-female-header-socket | Picked up from BELS

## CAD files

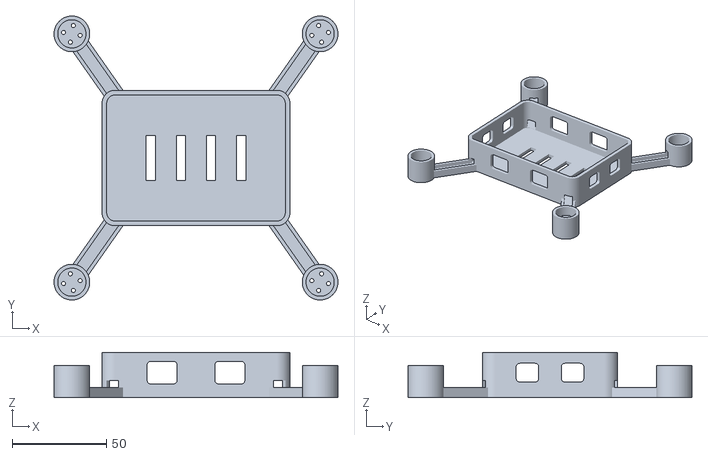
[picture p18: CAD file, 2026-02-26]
docs/drone-designs/drone-design-5/option-a/drone_design_5.stl
151.0 x 151.0 x 24.0

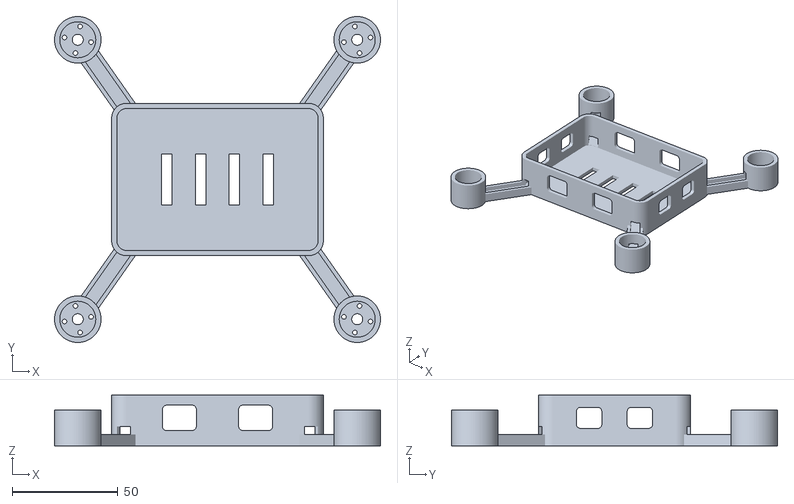
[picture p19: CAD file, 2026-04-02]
docs/drone-designs/drone-design-5/option-b/drone_design_5.stl
154.0 x 154.0 x 24.0

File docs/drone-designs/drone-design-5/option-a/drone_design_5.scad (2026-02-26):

/*
  ESP32-C3 drone frame (OpenSCAD model)
  - 3.5" to 4.0" prop-ready layout
  - SunnySky R1106 motors
  - ESP32-C3-DevKit-RUST-1 controller
*/

$fn = 80;

// Visual options
show_electronics_mockup = false;
show_esp32_header_pads = true;

// Main frame geometry (mm)
// v5 lightweight tuning: thinner shell while preserving electronics fit
body_length = 100;
body_width = 72;
body_height = 24;
body_corner_radius = 7;
floor_thickness = 2.5;
wall_thickness = 2.5;

// Motor layout (extended for larger prop options)
motor_center_offset = 66; // motor centers at (+/-x, +/-y)
arm_width = 10.0;
arm_thickness = 5.4;
arm_root_inset_x = 10;
arm_root_inset_y = 7;

// Motor pod geometry
motor_can_d = 14.2; // SunnySky R1106 rotor/body diameter
motor_can_l = 13.6; // SunnySky R1106 body length
motor_pod_outer_d = 19;
motor_pod_inner_d = 15.0; // +0.4 mm radial clearance per side for print tolerance
motor_pod_height = 17;
motor_mount_floor = 1.8;
motor_mount_bcd = 9; // SunnySky schematic: 4xM2 on 9 mm bolt-circle diameter
motor_mount_hole_center_r = motor_mount_bcd / 2;
motor_mount_hole_d = 2.2; // M2 clearance
motor_wire_notch_w = 6.2; // side opening for 3 motor wires
motor_wire_notch_h = 4.4;
motor_wire_notch_depth = 4.7; // deep enough to break through pod wall
enable_arm_frame_wire_notches = true;
arm_frame_wire_notch_w = 6.2;
arm_frame_wire_notch_h = 6.4;
arm_frame_wire_inboard_len = 8.0; // extend past arm root into frame pocket
arm_frame_wire_into_pod = 2.8; // start trench inside pod OD so cutout passes through pod wall

motor_pod_cavity_h = motor_pod_height - motor_mount_floor;
motor_pod_radial_clearance = (motor_pod_inner_d - motor_can_d) / 2;
motor_pod_axial_clearance = motor_pod_cavity_h - motor_can_l;

assert(motor_pod_radial_clearance >= 0.3, "Motor pod inner diameter too tight for SunnySky R1106.");
assert(motor_pod_axial_clearance >= 0.8, "Motor pod cavity height too short for SunnySky R1106.");

// ESP32-C3-DevKit-RUST-1 geometry from KiCad (mm)
// KiCad board X (22.86) is mapped to frame Y.
// KiCad board Y (63.50) is mapped to frame X.
esp32_board_kicad_x = 22.86;
esp32_board_kicad_y = 63.50;

esp32_corner_r_small = 0.508;
esp32_corner_r_top_right = 0.762;

esp32_hole_center_from_left = 2.54;
esp32_hole_center_from_bottom = 2.54;
esp32_hole_d = 3.048;

esp32_hole_spacing_x = esp32_board_kicad_y - 2 * esp32_hole_center_from_bottom; // 58.42
esp32_hole_spacing_y = esp32_board_kicad_x - 2 * esp32_hole_center_from_left; // 17.78

esp32_mount_hole_d = 3.25; // clearance around 3.048 mm board holes
esp32_standoff_d = 6;
esp32_standoff_h = 6;

// Strap slots in floor for battery hold-down
strap_slot_count = 4;
strap_slot_pitch = 16;
strap_slot_length = 5;
strap_slot_width = 24;

// Side-wall lightening windows
enable_side_lightening = true;
side_window_height = 12.0;
side_window_z_offset = 0.0; // fine-tune vertical position while keeping windows centered
long_side_window_length = 16.0;
long_side_window_x_offset = 18.0;
short_side_window_length = 10.0;
short_side_window_y_offset = 12.0;
side_window_corner_r = 2.0;

// Mock electronics (for fit visualization only)
esp32_board_length = esp32_board_kicad_y; // shown along frame X
esp32_board_width = esp32_board_kicad_x; // shown along frame Y
esp32_board_thickness = 1.6;
usb_c_overhang = 0.31; // from board edge using F.CrtYd
battery_connector_x = 2.54; // KiCad X
battery_connector_y = 31.75; // centered on board
battery_length = 70;
battery_width = 35;
battery_height = 24;

motor_to_motor_side = 2 * motor_center_offset;
motor_to_motor_diagonal = 2 * sqrt(2) * motor_center_offset;
inner_cavity_length = body_length - 2 * wall_thickness;
inner_cavity_width = body_width - 2 * wall_thickness;
inner_cavity_height = body_height - floor_thickness;
echo(str("motor_to_motor_side_mm=", motor_to_motor_side));
echo(str("motor_to_motor_diagonal_mm=", motor_to_motor_diagonal));
echo(str("inner_cavity_lwh_mm=", inner_cavity_length, "x", inner_cavity_width, "x", inner_cavity_height));
echo(str("motor_pod_radial_clearance_mm=", motor_pod_radial_clearance));
echo(str("motor_pod_axial_clearance_mm=", motor_pod_axial_clearance));
echo(str("esp32_hole_spacing_x_mm=", esp32_hole_spacing_x));
echo(str("esp32_hole_spacing_y_mm=", esp32_hole_spacing_y));

module rounded_rect_2d(l, w, r) {
    hull() {
        for (x = [-l / 2 + r, l / 2 - r], y = [-w / 2 + r, w / 2 - r]) {
            translate([x, y]) circle(r = r);
        }
    }
}

module rounded_box(l, w, h, r) {
    linear_extrude(height = h) rounded_rect_2d(l, w, r);
}

function arc_points(cx, cy, r, start_deg, end_deg, segments = 8) =
    [for (i = [0 : segments]) [cx + r * cos(start_deg + (end_deg - start_deg) * i / segments), cy + r * sin(start_deg + (end_deg - start_deg) * i / segments)]];

function esp32_outline_points() = concat(
    [[-esp32_board_length / 2 + esp32_corner_r_small, -esp32_board_width / 2]],
    [[esp32_board_length / 2 - esp32_corner_r_small, -esp32_board_width / 2]],
    arc_points(
        esp32_board_length / 2 - esp32_corner_r_small,
        -esp32_board_width / 2 + esp32_corner_r_small,
        esp32_corner_r_small,
        -90,
        0
    ),
    [[esp32_board_length / 2, esp32_board_width / 2 - esp32_corner_r_top_right]],
    arc_points(
        esp32_board_length / 2 - esp32_corner_r_top_right,
        esp32_board_width / 2 - esp32_corner_r_top_right,
        esp32_corner_r_top_right,
        0,
        90
    ),
    [[-esp32_board_length / 2 + esp32_corner_r_small, esp32_board_width / 2]],
    arc_points(
        -esp32_board_length / 2 + esp32_corner_r_small,
        esp32_board_width / 2 - esp32_corner_r_small,
        esp32_corner_r_small,
        90,
        180
    ),
    [[-esp32_board_length / 2, -esp32_board_width / 2 + esp32_corner_r_small]],
    arc_points(
        -esp32_board_length / 2 + esp32_corner_r_small,
        -esp32_board_width / 2 + esp32_corner_r_small,
        esp32_corner_r_small,
        180,
        270
    )
);

module esp32_board_2d() {
    polygon(points = esp32_outline_points());
}

module frame_arm(sx, sy) {
    root_x = sx * (body_length / 2 - arm_root_inset_x);
    root_y = sy * (body_width / 2 - arm_root_inset_y);
    motor_x = sx * motor_center_offset;
    motor_y = sy * motor_center_offset;

    hull() {
        translate([root_x, root_y, 0]) cylinder(h = arm_thickness, d = arm_width);
        translate([motor_x, motor_y, 0]) cylinder(h = arm_thickness, d = arm_width);
    }
}

module motor_pod(sx, sy) {
    motor_x = sx * motor_center_offset;
    motor_y = sy * motor_center_offset;
    translate([motor_x, motor_y, 0]) cylinder(h = motor_pod_height, d = motor_pod_outer_d);
}

module motor_wire_notch(mx, my, wire_angle) {
    // Keep notch above arm blend so the opening isn't blocked by the arm body.
    notch_z = max(
        motor_mount_floor + motor_wire_notch_h / 2 + 0.2,
        arm_thickness + motor_wire_notch_h / 2 + 0.3
    );
    notch_center_r = motor_pod_outer_d / 2 - motor_wire_notch_depth / 2 + 0.2;

    translate([mx, my, notch_z]) {
        rotate([0, 0, wire_angle]) {
            translate([notch_center_r, 0, 0]) {
                cube([motor_wire_notch_depth, motor_wire_notch_w, motor_wire_notch_h], center = true);
            }
        }
    }
}

module arm_to_frame_wire_notch(sx, sy) {
    root_x = sx * (body_length / 2 - arm_root_inset_x);
    root_y = sy * (body_width / 2 - arm_root_inset_y);
    motor_x = sx * motor_center_offset;
    motor_y = sy * motor_center_offset;

    dir_x = root_x - motor_x;
    dir_y = root_y - motor_y;
    dir_len = sqrt(dir_x * dir_x + dir_y * dir_y);
    ux = dir_x / dir_len;
    uy = dir_y / dir_len;

    // Keep this trench high enough to be open at the arm top and into the frame pocket.
    notch_z = max(
        arm_thickness - arm_frame_wire_notch_h / 2 + 0.1,
        floor_thickness + arm_frame_wire_notch_h / 2 + 0.2
    );

    start_r = max(0, motor_pod_outer_d / 2 - arm_frame_wire_into_pod);
    start_x = motor_x + ux * start_r;
    start_y = motor_y + uy * start_r;
    frame_x = root_x + ux * arm_frame_wire_inboard_len;
    frame_y = root_y + uy * arm_frame_wire_inboard_len;
    notch_len = sqrt((frame_x - start_x) * (frame_x - start_x) + (frame_y - start_y) * (frame_y - start_y));
    notch_angle = atan2(frame_y - start_y, frame_x - start_x);

    translate([(start_x + frame_x) / 2, (start_y + frame_y) / 2, notch_z]) {
        rotate([0, 0, notch_angle]) {
            cube([notch_len, arm_frame_wire_notch_w, arm_frame_wire_notch_h], center = true);
        }
    }
}

module side_lightening_cutouts() {
    side_window_z = floor_thickness + (body_height - floor_thickness) / 2 + side_window_z_offset;
    side_cut_depth = wall_thickness + 1.0;
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

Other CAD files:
docs/drone-designs/drone-design-5/option-a/drone_design_5.gcode.3mf
docs/drone-designs/drone-design-5/option-b/drone_design_5.gcode.3mf
docs/drone-designs/drone-design-5/option-b/drone_design_5.scad

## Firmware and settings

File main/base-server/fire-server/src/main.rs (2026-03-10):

use std::fs::OpenOptions;
use std::io::{Read, Write as IoWrite};
use std::net::{TcpListener, TcpStream};
use std::str::FromStr;
use std::thread;

#[derive(Debug)]
struct FireTelemetry {
    drone_id: String,
    fire_detected: bool,
    fire_distance_m: f32,
    fire_range_m: f32,
    temperature_c: f32,
    humidity_pct: f32,
}

fn parse_request_line(line: &str) -> Result<(), String> {
    // Expect: METHOD PATH VERSION, e.g. "FIRE /telemetry DRONE/1.0"
    let parts: Vec<&str> = line.trim_end().split_whitespace().collect();
    if parts.len() != 3 {
        return Err("invalid request line".into());
    }
    let method = parts[0];
    let path = parts[1];
    let version = parts[2];

    if method != "FIRE" {
        return Err("unsupported method".into());
    }
    if path != "/telemetry" {
        return Err("unsupported path".into());
    }
    if !version.starts_with("DRONE/") {
        return Err("unsupported version".into());
    }
    Ok(())
}

fn parse_telemetry_line(line: &str) -> Result<FireTelemetry, String> {
    // Example:
    // "Fire-Detected: yes; Fire-Distance: 120; Fire-Range: 45; Temperature: 63.4; Humidity: 21.5; Drone-ID: DRONE-01"
    let mut drone_id: Option<String> = None;
    let mut fire_detected = None;
    let mut fire_distance_m = None;
    let mut fire_range_m = None;
    let mut temperature_c = None;
    let mut humidity_pct = None;

    for part in line.trim_end().split(';') {
        let kv = part.trim();
        if kv.is_empty() {
            continue;
        }
        let mut iter = kv.splitn(2, ':');
        let key = iter.next().ok_or("missing key")?.trim();
        let value = iter.next().ok_or("missing value")?.trim();

        match key {
            "Fire-Detected" => {
                fire_detected = Some(match value {
                    "yes" | "YES" | "Yes" => true,
                    "no" | "NO" | "No" => false,
                    _ => return Err("invalid Fire-Detected value".into()),
                });
            }
            "Fire-Distance" => {
                fire_distance_m = Some(f32::from_str(value).map_err(|_| "invalid Fire-Distance")?);
            }
            "Fire-Range" => {
                fire_range_m = Some(f32::from_str(value).map_err(|_| "invalid Fire-Range")?);
            }
            "Temperature" => {
                temperature_c = Some(f32::from_str(value).map_err(|_| "invalid Temperature")?);
            }
            "Humidity" => {
                humidity_pct = Some(f32::from_str(value).map_err(|_| "invalid Humidity")?);
            }
            "Drone-ID" => {
                drone_id = Some(value.to_string());
            }
            _ => {
                // Ignore unknown keys
            }
        }
    }

    Ok(FireTelemetry {
        drone_id: drone_id.ok_or("missing Drone-ID")?,
        fire_detected: fire_detected.ok_or("missing Fire-Detected")?,
        fire_distance_m: fire_distance_m.ok_or("missing Fire-Distance")?,
        fire_range_m: fire_range_m.ok_or("missing Fire-Range")?,
        temperature_c: temperature_c.ok_or("missing Temperature")?,
        humidity_pct: humidity_pct.ok_or("missing Humidity")?,
    })
}

fn log_telemetry(t: &FireTelemetry) -> std::io::Result<()> {
    let mut file = OpenOptions::new()
        .append(true)
        .create(true)
        .open("telemetry.log")?;

    // Simple CSV-style line: drone_id, fire_detected, distance, range, temp, humidity
    writeln!(
        &mut file,
        "{}, {}, {:.2}, {:.2}, {:.2}, {:.2}",
        t.drone_id,
        if t.fire_detected { "yes" } else { "no" },
        t.fire_distance_m,
        t.fire_range_m,
        t.temperature_c,
        t.humidity_pct
    )?;
    Ok(())
}

fn handle_client(mut stream: TcpStream) {
    let mut buf = [0u8; 1024];
    let n = match stream.read(&mut buf) {
        Ok(0) => return,
        Ok(n) => n,
        Err(_) => return,
    };

    let received = match std::str::from_utf8(&buf[..n]) {
        Ok(s) => s,
        Err(_) => {
            let _ = stream.write_all(b"DRONE/1.0 400 FAIL\n\n");
            return;
        }
    };

    // Accept '\n' (nc/manual typing) and also handles '\r\n'
    let mut lines = received.lines();

    let request_line = match lines.next() {
        Some(l) if !l.is_empty() => l,
        _ => {
            let _ = stream.write_all(b"DRONE/1.0 400 FAIL\n\n");
            return;
        }
    };

    if let Err(e) = parse_request_line(request_line) {
        eprintln!("Bad request line: {e}");
        let _ = stream.write_all(b"DRONE/1.0 400 FAIL\n\n");
        return;
    }

    let telemetry_line = match lines.next() {
        Some(l) if !l.is_empty() => l,
        _ => {
            let _ = stream.write_all(b"DRONE/1.0 400 FAIL\n\n");
            return;
        }
    };

    match parse_telemetry_line(telemetry_line) {
        Ok(t) => {
            println!("Drone ID: {}", t.drone_id);
            println!("Fire Detected: {}", if t.fire_detected { "yes" } else { "no" });
            println!("Fire Distance: {:.2} meters", t.fire_distance_m);
            println!("Fire Range: {:.2} meters", t.fire_range_m);
            println!("Temperature: {:.2} C", t.temperature_c);
            println!("Humidity: {:.2} %", t.humidity_pct);
            println!("--------------------------------");

            if let Err(e) = log_telemetry(&t) {
                eprintln!("Failed to log telemetry: {e}");
            }

            let _ = stream.write_all(b"DRONE/1.0 200 OK\n\n");
        }
        Err(e) => {
            eprintln!("Parse error: {e}");
            let _ = stream.write_all(b"DRONE/1.0 400 FAIL\n\n");
        }
    }
}

fn main() -> std::io::Result<()> {
    let listener = TcpListener::bind("0.0.0.0:7878")?;
    println!("Listening on 0.0.0.0:7878...");

    for stream in listener.incoming() {
        match stream {
            Ok(stream) => {
                thread::spawn(|| handle_client(stream));
            }
            Err(e) => eprintln!("Connection failed: {e}"),
        }
    }
    Ok(())
}

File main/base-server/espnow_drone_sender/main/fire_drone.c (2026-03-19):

#include <stdio.h>
#include <string.h>
#include <stdbool.h>

#include "freertos/FreeRTOS.h"
#include "freertos/task.h"

#include "esp_wifi.h"
#include "esp_now.h"
#include "esp_event.h"
#include "esp_log.h"
#include "nvs_flash.h"

#include "driver/i2c.h"

static const char *TAG = "ESP_NOW_DRONE";

// CHANGE THIS to match the bridge log
static uint8_t BRIDGE_MAC[ESP_NOW_ETH_ALEN] = { 0xA0, 0x85, 0xE3, 0x06, 0x38, 0xE8 };

// Onboard SHTC3 temp/humidity sensor on the ESP32-C3-DevKit-RUST-1
// I2C address and pins from board docs:
#define I2C_PORT_NUM       I2C_NUM_0
#define I2C_SCL_IO         GPIO_NUM_8    // SCL
#define I2C_SDA_IO         GPIO_NUM_10   // SDA
#define I2C_FREQ_HZ        100000
#define SHTC3_ADDR         0x70

// SHTC3 commands (no clock stretching, single-shot, high precision)
#define SHTC3_CMD_WAKEUP           0x3517
#define SHTC3_CMD_SLEEP            0xB098
#define SHTC3_CMD_MEASURE_TFIRST   0x7866  // measure T first, then RH (no clock stretching)

static esp_err_t i2c_master_init(void)
{
    i2c_config_t conf = {
        .mode = I2C_MODE_MASTER,
        .sda_io_num = I2C_SDA_IO,
        .scl_io_num = I2C_SCL_IO,
        .sda_pullup_en = GPIO_PULLUP_ENABLE,
        .scl_pullup_en = GPIO_PULLUP_ENABLE,
        .master.clk_speed = I2C_FREQ_HZ,
    };
    ESP_ERROR_CHECK(i2c_param_config(I2C_PORT_NUM, &conf));
    ESP_ERROR_CHECK(i2c_driver_install(I2C_PORT_NUM, conf.mode, 0, 0, 0));
    return ESP_OK;
}

static esp_err_t shtc3_write_cmd(uint16_t cmd)
{
    uint8_t buf[2] = { (uint8_t)(cmd >> 8), (uint8_t)(cmd & 0xFF) };

    i2c_cmd_handle_t handle = i2c_cmd_link_create();
    i2c_master_start(handle);
    i2c_master_write_byte(handle, (SHTC3_ADDR << 1) | I2C_MASTER_WRITE, true);
    i2c_master_write(handle, buf, 2, true);
    i2c_master_stop(handle);
    esp_err_t ret = i2c_master_cmd_begin(I2C_PORT_NUM, handle, pdMS_TO_TICKS(100));
    i2c_cmd_link_delete(handle);
    return ret;
}

// Read temperature (°C) and humidity (%RH) from SHTC3
static esp_err_t shtc3_read_temp_humidity(float *temperature_c, float *humidity_rh)
{
    esp_err_t ret;

    // Wake up sensor
    ret = shtc3_write_cmd(SHTC3_CMD_WAKEUP);
    if (ret != ESP_OK) {
        ESP_LOGW(TAG, "SHTC3 wakeup failed: %s", esp_err_to_name(ret));
        return ret;
    }
    vTaskDelay(pdMS_TO_TICKS(5));

    // Trigger measurement (temperature first, then humidity)
    ret = shtc3_write_cmd(SHTC3_CMD_MEASURE_TFIRST);
    if (ret != ESP_OK) {
        ESP_LOGW(TAG, "SHTC3 measure command failed: %s", esp_err_to_name(ret));
        return ret;
    }

    // Measurement time: ~12ms typical; use 30ms to be safe
    vTaskDelay(pdMS_TO_TICKS(30));

    // Read 6 bytes: T_MSB, T_LSB, T_CRC, RH_MSB, RH_LSB, RH_CRC
    uint8_t data[6] = {0};
    i2c_cmd_handle_t handle = i2c_cmd_link_create();
    i2c_master_start(handle);
    i2c_master_write_byte(handle, (SHTC3_ADDR << 1) | I2C_MASTER_READ, true);
    i2c_master_read(handle, data, 6, I2C_MASTER_LAST_NACK);
    i2c_master_stop(handle);
    ret = i2c_master_cmd_begin(I2C_PORT_NUM, handle, pdMS_TO_TICKS(100));
    i2c_cmd_link_delete(handle);
    if (ret != ESP_OK) {
        ESP_LOGW(TAG, "SHTC3 read failed: %s", esp_err_to_name(ret));
        return ret;
    }

    uint16_t raw_t = ((uint16_t)data[0] << 8) | data[1];
    uint16_t raw_rh = ((uint16_t)data[3] << 8) | data[4];

    // Convert raw values to physical units (from SHTC3 datasheet)
    *temperature_c = -45.0f + 175.0f * ((float)raw_t / 65535.0f);
    *humidity_rh = 100.0f * ((float)raw_rh / 65535.0f);

    return ESP_OK;
}

static void espnow_send_cb(const esp_now_send_info_t *tx_info, esp_now_send_status_t status)
{
    const uint8_t *mac_addr = tx_info->des_addr;
    ESP_LOGI(TAG, "Send status to %02X:%02X:%02X:%02X:%02X:%02X -> %s",
             mac_addr[0], mac_addr[1], mac_addr[2],
             mac_addr[3], mac_addr[4], mac_addr[5],
             status == ESP_NOW_SEND_SUCCESS ? "SUCCESS" : "FAIL");
}

static void init_wifi_espnow_and_i2c(void)
{
    // Initialize NVS
    esp_err_t ret = nvs_flash_init();
    if (ret == ESP_ERR_NVS_NO_FREE_PAGES || ret == ESP_ERR_NVS_NEW_VERSION_FOUND) {
        ESP_ERROR_CHECK(nvs_flash_erase());
        ESP_ERROR_CHECK(nvs_flash_init());
    }

    // Initialize TCP/IP and event loop
    ESP_ERROR_CHECK(esp_netif_init());
    ESP_ERROR_CHECK(esp_event_loop_create_default());

    // Initialize Wi-Fi in STA mode
    wifi_init_config_t cfg = WIFI_INIT_CONFIG_DEFAULT();
    ESP_ERROR_CHECK(esp_wifi_init(&cfg));
    ESP_ERROR_CHECK(esp_wifi_set_mode(WIFI_MODE_STA));
    ESP_ERROR_CHECK(esp_wifi_start());

    uint8_t mac[6];
    ESP_ERROR_CHECK(esp_wifi_get_mac(WIFI_IF_STA, mac));
    ESP_LOGI(TAG, "Drone STA MAC: %02X:%02X:%02X:%02X:%02X:%02X",
             mac[0], mac[1], mac[2], mac[3], mac[4], mac[5]);

    // Initialize I2C for SHTC3
    ESP_ERROR_CHECK(i2c_master_init());
    ESP_LOGI(TAG, "I2C initialized for SHTC3");

    // Initialize ESP-NOW
    ESP_ERROR_CHECK(esp_now_init());
    ESP_ERROR_CHECK(esp_now_register_send_cb(espnow_send_cb));
    ESP_LOGI(TAG, "ESP-NOW initialized");

    // Add bridge as peer
    esp_now_peer_info_t peer = {0};
    memcpy(peer.peer_addr, BRIDGE_MAC, ESP_NOW_ETH_ALEN);
    peer.channel = 0;      // use current Wi-Fi channel
    peer.encrypt = false;  // no encryption for now

    ESP_ERROR_CHECK(esp_now_add_peer(&peer));
    ESP_LOGI(TAG, "Bridge peer added");
}
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

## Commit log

2026-02-24 Motor Demo
2026-02-24 clean up
    [drone_design_5.gcode.3mf, drone_design_5.scad, drone_design_5.stl]
2026-02-24 Design Doc v3 (switched to pdf upload)
    Reformatted Document to match requirements and clean up
    Added Title Page with Logos and Names
    Added Executive Summary
    Added Need Statement
    Added Goal Statement
    Added Existing Research Section
2026-02-24 Add prototype script for drone project
2026-02-24 Drone Design Schematic
2026-02-26 drone_design_5 update
    [drone_design_5.gcode.3mf, drone_design_5.scad, drone_design_5.stl]
2026-02-27 Update Parsa's status with recent tasks
    Added updates for Parsa's tasks including SHTC3 sensor setup and design document edits.
2026-03-03 Enhance sustainability and design sections in document
    Added sustainability statements and design considerations for the FireFly project, including environmental stewardship, material selection, and safety impact.
2026-03-03 Update design-document_final.tex
    added high level design schematic image
2026-03-03 Circuit Diagram
2026-03-03 Add wiring diagrams section with circuit diagram
2026-03-03 Revise technology and simulations sections for clarity
    Updated the technology section to reflect the new ESP32-C3 architecture and ESP-NOW protocol. Enhanced the simulations section to clarify the mission requirements and confirm the hardware's capabilit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
2026-03-03 Add circuit diagram to wiring diagrams section
2026-03-03 scripts for ble and using the imu with spi
2026-03-03 Add aesthetic prototype and DFM/DFA details
    Expanded the Design section
2026-03-06 Speed control update with potentiometer
    connected a potentiometer to pwm pin on the esp to get control over how much voltage was being sent through to the motor controlling the speed. The potentiometer turns the motor off at the mid point 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
2026-03-10 organized files
    [bill_of_materials_v1.csv, bill_of_materials_v2.csv, bill_of_materials_v3.csv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]
2026-03-10 Implement TCP client for telemetry data transmission
    This file implements a client that connects to a TCP server, sends telemetry data, and prints the server's response.
2026-03-10 Enhance Q&A backup one-liner for blinking LED
    Added clarification on the blinking LED's function in the prototype test.
2026-03-10 Update backup one-liners for Q&A section
    Clarified responses for Q&A regarding prototype testing.
2026-03-11 Revise prototype communication path and evidence
    Updated the prototype description to clarify the communication path and the visible proof of functionality.
2026-03-11 Revise script prototype for clarity and structure
2026-03-11 Refine testing plan description and prototype outcome
    Removed redundancy in the description of the testing plan and clarified the prototype's successful response.
2026-03-11 Revise prototype demonstration description
    Clarified the statement regarding the prototype demonstration.
2026-03-11 Update script prototype notes for clarity
    Removed outdated information about the phone or app stage due to instability in communication. Clarified the components of the current prototype for better understanding.
2026-03-11 Last Instructor Meeting
    Going over script and schematic design changes
2026-03-11 motor spin
2026-03-11 changes made to motor reciever
2026-03-11 Update build config for ADC
2026-03-13 Add ESP-NOW bridge with UART communication
    Implement ESP-NOW bridge functionality with UART output.
2026-03-13 Add ESP-NOW drone sender implementation
    This file implements the ESP-NOW drone sender functionality, including I2C initialization for the SHTC3 sensor, temperature and humidity reading, and sending telemetry data.
2026-03-13 Final Schematic
2026-03-13 updated final schematic
2026-03-19 staging shtc3 sensor data
2026-04-02 drone design 5 option b (motors)
    [drone_design_5.gcode.3mf, drone_design_5.scad, drone_design_5.stl]
